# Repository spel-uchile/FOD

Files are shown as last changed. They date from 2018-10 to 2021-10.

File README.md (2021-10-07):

# Femto-satellite Orbital Deployer (FOD)

This repository contains the PCB design and the source code of a femto-satellite orbital deployer or FOD. This device works by cutting a fishing line with Nichrome wire. The fishing line is normally pressing a hinge lever. When the line is cut, the hinge lever is released end the microcontroller can detect the release status.

The PCB has a transceiver (NRF24L01) to communicate with the femto-satellite once it is released. There is also a LED showing the release status, and a reset button. The energy and the comunication with the OBC is done through a molex cable with a picoblade connector.

This new version is designed for CubeSats of 2U or more. It is intended to be used as a type A interstage panel, so that it leaves more space inside the CubeSat for other payloads.

Current version: 4.0.0

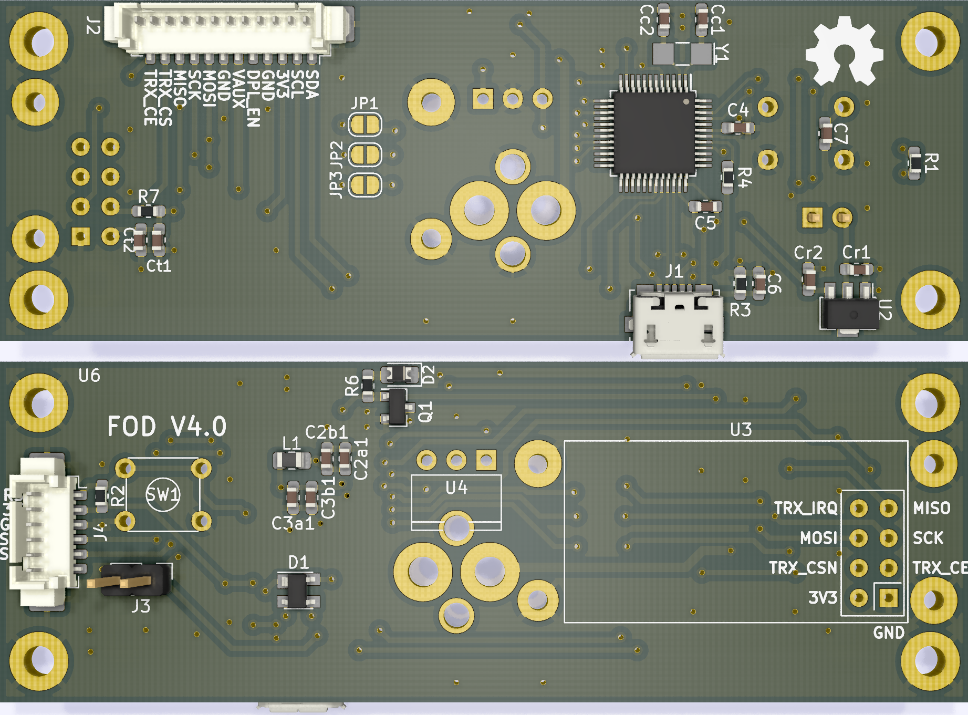
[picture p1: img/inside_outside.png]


### Supported software:

* KiCAD 5.99.0

### Supported hardware:

* Microcontroller: ATSAMD21G18
* Transceiver: NRF24L01
* Hinge lever: AV4524
* Mosfet: PMV16XNR

### Contact:

* Name: Matías Vidal Valladares
* e-mail: matias.vidal.v@gmail.com

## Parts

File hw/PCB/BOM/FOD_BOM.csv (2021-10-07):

Comment | Designator | Footprint | JLCPCB Part #
10uF 0603, C1608X5R0J106K080AE | C2a1, C3a1, Ct2 | Capacitor_SMD:C_0603_1608Metric_Pad1.05x0.95mm_HandSolder | C267437
100nF 0603, 06036C104JAT2A | C2b1, C3b1, C5, C7, Ct1 | Capacitor_SMD:C_0603_1608Metric_Pad1.05x0.95mm_HandSolder
1uF 0603, C0603X105J9RACAUTO | C4, Cr1, Cr2 | Capacitor_SMD:C_0603_1608Metric_Pad1.05x0.95mm_HandSolder
4.7nF 0603, C0603C472K9RACTU | C6 | Capacitor_SMD:C_0603_1608Metric_Pad1.05x0.95mm_HandSolder
9pF 0603, 06033A9R0CAT2A | Cc1, Cc2 | Capacitor_SMD:C_0603_1608Metric_Pad1.05x0.95mm_HandSolder
PRTR5V0U2X,215 | D1 | Package_TO_SOT_SMD:SOT-143 | C12333
Green LED 0805 | D2 | Diode_SMD:D_0805_2012Metric_Pad1.15x1.40mm_HandSolder | C397047
USB_B_Micro, ZX62-AB-5PA(31) | J1 | Connector_USB:USB_Micro-B_Molex_47346-0001 | C2692071
Molex PicoBlade SMD 1x12, 53398-1271 | J2 | Connector_Molex:Molex_PicoBlade_53398-1271_1x12-1MP_P1.25mm_Vertical
Pin header 1x2 | J3 | Connector_PinHeader_2.54mm:PinHeader_1x02_P2.54mm_Vertical
Molex PicoBlade SMD 1x6, 53398-0671 | J4 | Connector_Molex:Molex_PicoBlade_53398-0671_1x06-1MP_P1.25mm_Vertical
Jumper | JP1, JP2, JP3 | Jumper:SolderJumper-2_P1.3mm_Open_RoundedPad1.0x1.5mm
Ferrite_Bead, MPZ2012S221AT000 | L1 | Inductor_SMD:L_0805_2012Metric_Pad1.15x1.40mm_HandSolder | C76818
PMV16XNR | Q1 | Package_TO_SOT_SMD:SOT-23 | C110920
1k 0603, RC0603FR-071KL | R1, R7 | Resistor_SMD:R_0603_1608Metric_Pad1.05x0.95mm_HandSolder
10k 0603, ESR03EZPF1002 | R2 | Resistor_SMD:R_0603_1608Metric_Pad1.05x0.95mm_HandSolder | C253330
1M 0603, ESR03EZPF1004 | R3 | Resistor_SMD:R_0603_1608Metric_Pad1.05x0.95mm_HandSolder | C253332
330, CRGH0603F330R | R4, R6 | Resistor_SMD:R_0603_1608Metric_Pad1.05x0.95mm_HandSolder
Reset_push | SW1 | Button_Switch_THT:SW_TH_Tactile_Omron_B3F-10xx | C231317
ATSAMD21G18A-AFT | U1 | Package_QFP:TQFP-48_7x7mm_P0.5mm | C78624
AP7215-33YG-13 | U2 | Package_TO_SOT_SMD:SOT-89-3 | C460367
AV4524 | U4 | Interrupt:AV4524
32.768kHz, ECS-.327-9-34QCS-TR | Y1 | Crystal:Crystal_SMD_EuroQuartz_EQ161-2Pin_3.2x1.5mm_HandSoldering

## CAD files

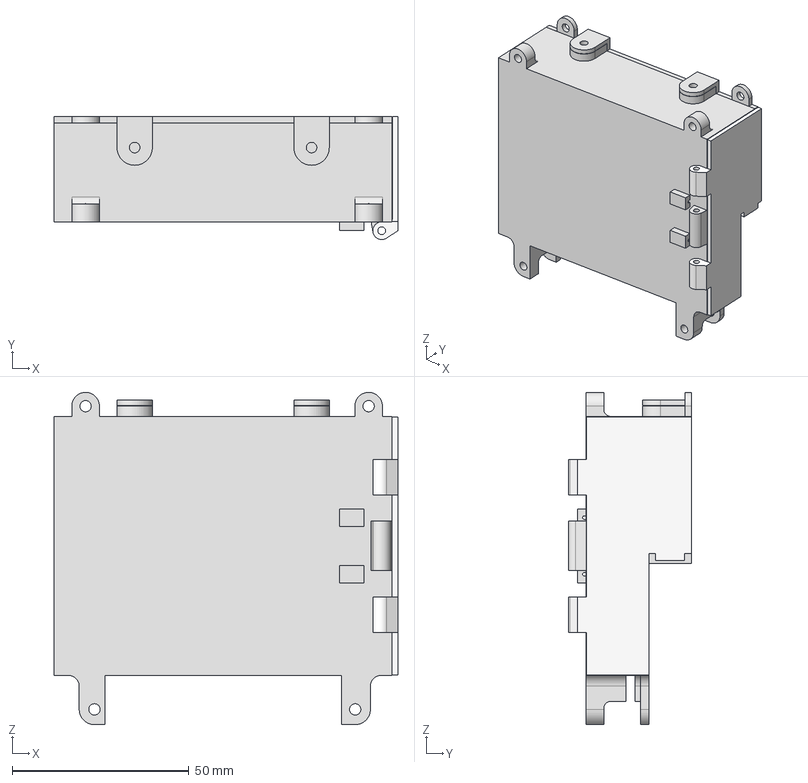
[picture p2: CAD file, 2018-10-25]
hw/CAD/Ensamble_rev1.stp
97.2 x 34.8 x 93.9 mm
Base_FOD
Tapa_FOD
Tapa_frental_FOD

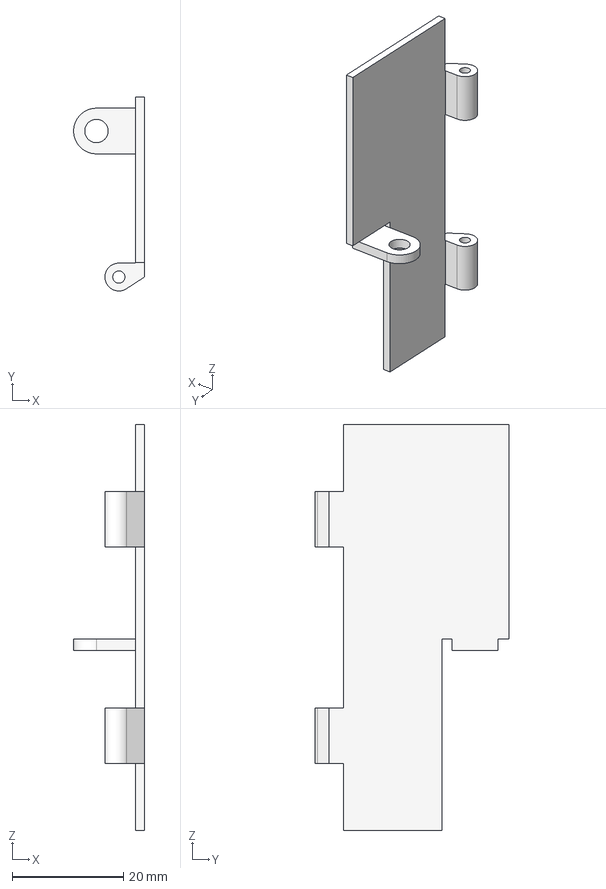
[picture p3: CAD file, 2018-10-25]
hw/CAD/Tapa_FOD.stp
12.7 x 34.8 x 72.8 mm

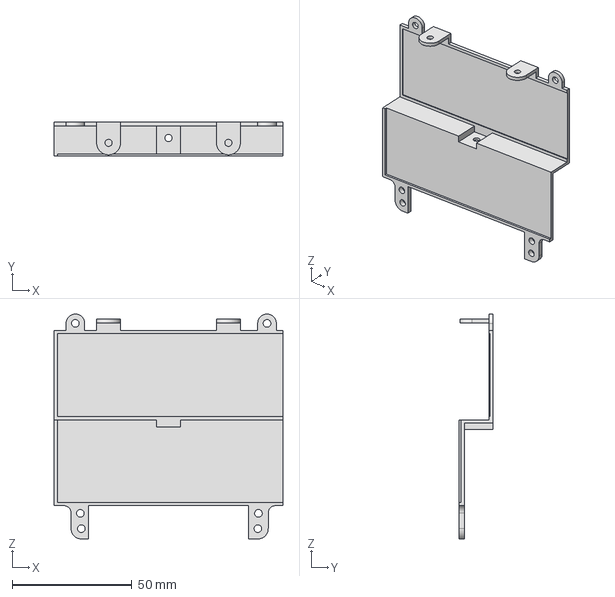
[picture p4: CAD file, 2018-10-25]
hw/CAD/Techo_FOD.stp
95.6 x 14.4 x 93.9 mm

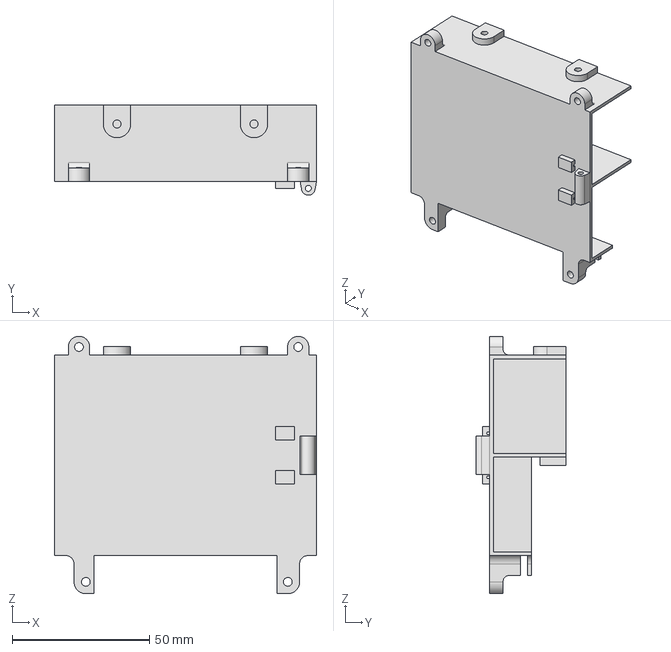
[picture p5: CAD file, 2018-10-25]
hw/CAD/Base_FOD.stp
95.6 x 33.0 x 93.9 mm

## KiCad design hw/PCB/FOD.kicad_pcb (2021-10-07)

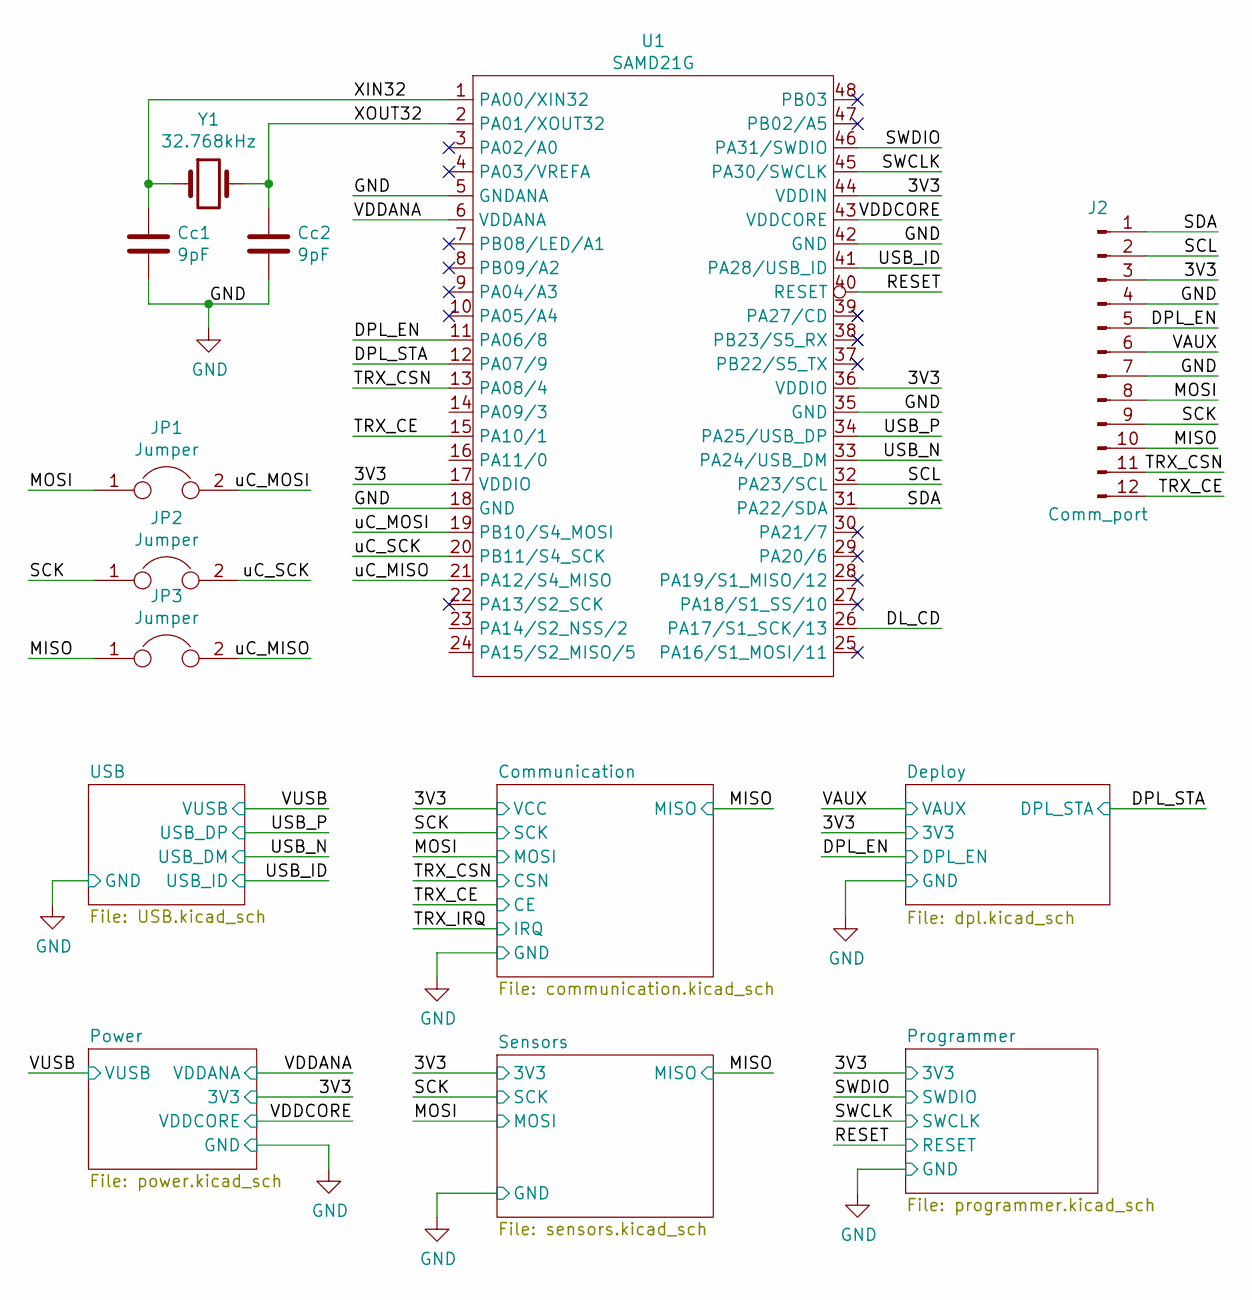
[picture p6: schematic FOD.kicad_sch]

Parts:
Cc1, Cc2: 9pF; C_0603_1608Metric_Pad1.05x0.95mm_HandSolder
J2: Comm_port; Molex_PicoBlade_53398-1271_1x12-1MP_P1.25mm_Vertical
JP1, JP2, JP3: Jumper; SolderJumper-2_P1.3mm_Open_RoundedPad1.0x1.5mm
U1: SAMD21G; TQFP-48_7x7mm_P0.5mm
Y1: 32.768kHz; Crystal_SMD_EuroQuartz_EQ161-2Pin_3.2x1.5mm_HandSoldering

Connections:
/3V3: J2.3, U1.17 (VDDIO), U1.36 (VDDIO), U1.44 (VDDIN); also elsewhere on the board
/DL_CD: U1.26 (PA17/S1_SCK/13)
/DPL_EN: J2.5, U1.11 (PA06/8); also elsewhere on the board
/DPL_STA: U1.12 (PA07/9); also elsewhere on the board
/MISO: J2.10, JP3.1; also elsewhere on the board
/MOSI: J2.8, JP1.1; also elsewhere on the board
/RESET: U1.40 (RESET); also elsewhere on the board
/SCK: J2.9, JP2.1; also elsewhere on the board
/SCL: J2.2, U1.32 (PA23/SCL)
/SDA: J2.1, U1.31 (PA22/SDA)
/SWCLK: U1.45 (PA30/SWCLK); also elsewhere on the board
/SWDIO: U1.46 (PA31/SWDIO); also elsewhere on the board
/TRX_CE: J2.12, U1.15 (PA10/1); also elsewhere on the board
/TRX_CSN: J2.11, U1.13 (PA08/4); also elsewhere on the board
/USB_ID: U1.41 (PA28/USB_ID); also elsewhere on the board
/USB_N: U1.33 (PA24/USB_DM); also elsewhere on the board
/USB_P: U1.34 (PA25/USB_DP); also elsewhere on the board
/VAUX: J2.6; also elsewhere on the board
/VDDANA: U1.6 (VDDANA); also elsewhere on the board
/VDDCORE: U1.43 (VDDCORE); also elsewhere on the board
/XIN32: Cc1.1, U1.1 (PA00/XIN32), Y1.1
/XOUT32: Cc2.1, U1.2 (PA01/XOUT32), Y1.2
/uC_MISO: JP3.2, U1.21 (PA12/S4_MISO)
/uC_MOSI: JP1.2, U1.19 (PB10/S4_MOSI)
/uC_SCK: JP2.2, U1.20 (PB11/S4_SCK)
GND: Cc1.2, Cc2.2, J2.4, J2.7, J2.MP, U1.5 (GNDANA), U1.18 (GND), U1.35 (GND), U1.42 (GND); also elsewhere on the board

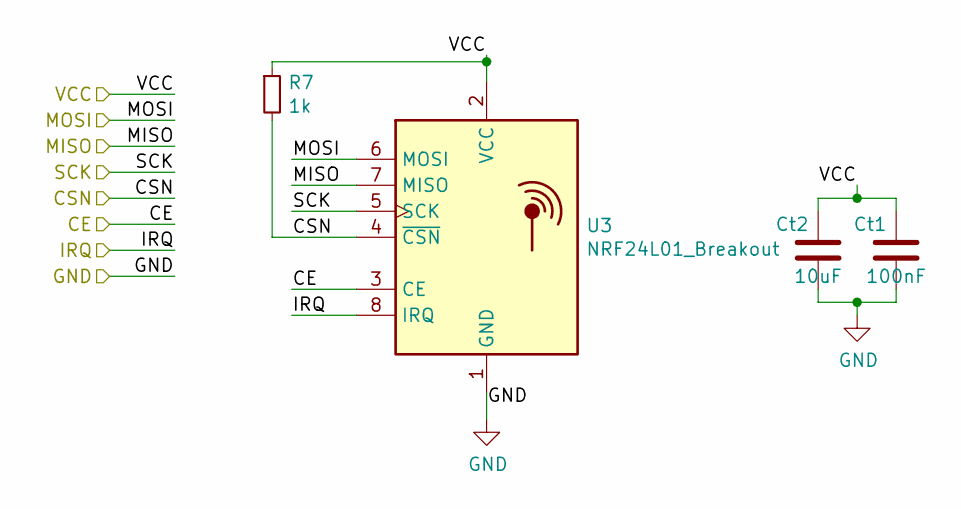
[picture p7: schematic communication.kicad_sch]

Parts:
Ct1: 100nF; C_0603_1608Metric_Pad1.05x0.95mm_HandSolder
Ct2: 10uF; C_0603_1608Metric_Pad1.05x0.95mm_HandSolder
R7: 1k; R_0603_1608Metric_Pad1.05x0.95mm_HandSolder
U3: NRF24L01_Breakout; nRF24L01_Breakout

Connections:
/3V3: Ct1.2, Ct2.2, R7.1, U3.2 (VCC); also elsewhere on the board
/MISO: U3.7 (MISO); also elsewhere on the board
/MOSI: U3.6 (MOSI); also elsewhere on the board
/SCK: U3.5 (SCK); also elsewhere on the board
/TRX_CE: U3.3 (CE); also elsewhere on the board
/TRX_CSN: R7.2, U3.4 (~CSN); also elsewhere on the board
/TRX_IRQ: U3.8 (IRQ)
GND: Ct1.1, Ct2.1, U3.1 (GND); also elsewhere on the board

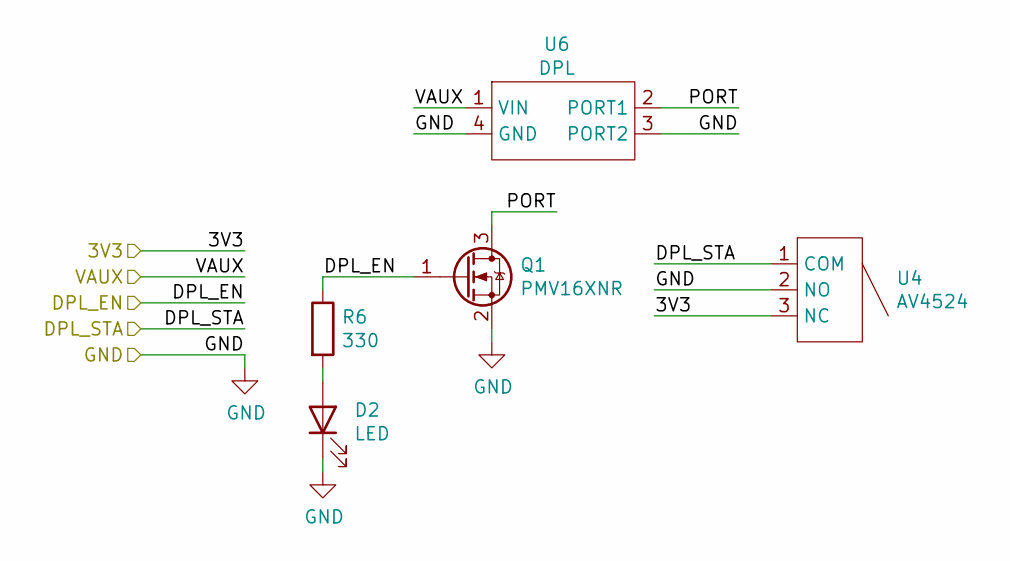
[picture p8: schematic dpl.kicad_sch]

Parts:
D2: LED; D_0805_2012Metric_Pad1.15x1.40mm_HandSolder
Q1: PMV16XNR; SOT-23
R6: 330; R_0603_1608Metric_Pad1.05x0.95mm_HandSolder
U4: AV4524
U6: DPL; Type-A_middle_port

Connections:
/3V3: U4.3 (NC); also elsewhere on the board
/DPL_EN: Q1.1 (G), R6.1; also elsewhere on the board
/DPL_STA: U4.1 (COM); also elsewhere on the board
/Deploy/PORT: Q1.3 (D), U6.2 (PORT1)
/VAUX: U6.1 (VIN); also elsewhere on the board
GND: D2.1 (K), Q1.2 (S), U4.2 (NO), U6.3 (PORT2), U6.4 (GND); also elsewhere on the board
unnamed: D2.2 (A), R6.2

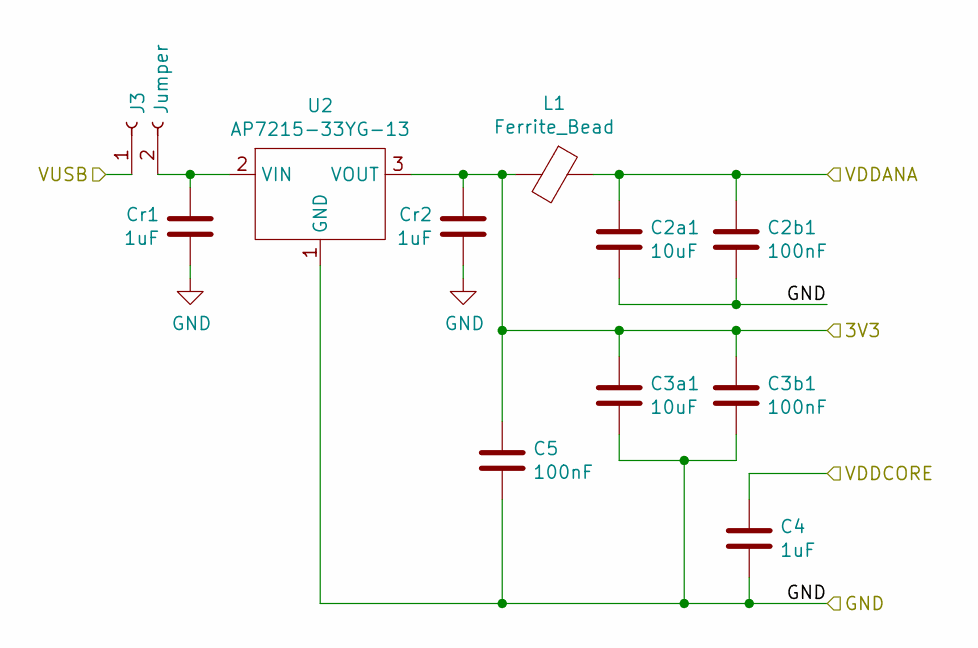
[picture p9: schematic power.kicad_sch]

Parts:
C2a1, C3a1: 10uF; C_0603_1608Metric_Pad1.05x0.95mm_HandSolder
C2b1, C3b1, C5: 100nF; C_0603_1608Metric_Pad1.05x0.95mm_HandSolder
C4: 1uF; C_0603_1608Metric_Pad1.05x0.95mm_HandSolder
Cr1, Cr2: 1uF; C_0603_1608Metric_Pad1.05x0.95mm_HandSolder
J3: Jumper; PinHeader_1x02_P2.54mm_Vertical
L1: Ferrite_Bead; L_0805_2012Metric_Pad1.15x1.40mm_HandSolder
U2: AP7215-33YG-13; SOT-89-3

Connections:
/3V3: C3a1.1, C3b1.1, C5.1, Cr2.1, L1.2, U2.3 (VOUT); also elsewhere on the board
/VDDANA: C2a1.1, C2b1.1, L1.1; also elsewhere on the board
/VDDCORE: C4.1; also elsewhere on the board
/VUSB: J3.1; also elsewhere on the board
GND: C2a1.2, C2b1.2, C3a1.2, C3b1.2, C4.2, C5.2, Cr1.2, Cr2.2, U2.1 (GND); also elsewhere on the board
unnamed: Cr1.1, J3.2, U2.2 (VIN)

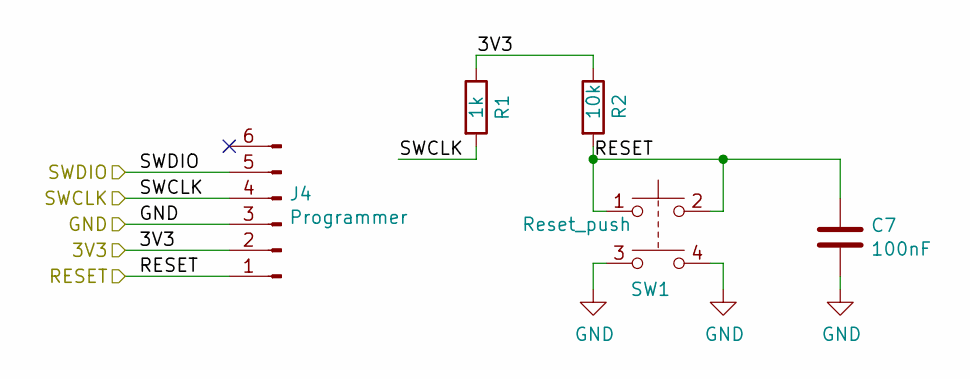
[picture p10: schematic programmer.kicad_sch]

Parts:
C7: 100nF; C_0603_1608Metric_Pad1.05x0.95mm_HandSolder
J4: Programmer; Molex_PicoBlade_53398-0671_1x06-1MP_P1.25mm_Vertical
R1: 1k; R_0603_1608Metric_Pad1.05x0.95mm_HandSolder
R2: 10k; R_0603_1608Metric_Pad1.05x0.95mm_HandSolder
SW1: Reset_push; SW_TH_Tactile_Omron_B3F-10xx

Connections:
/3V3: J4.2, R1.1, R2.1; also elsewhere on the board
/RESET: C7.1, J4.1, R2.2, SW1.1, SW1.2; also elsewhere on the board
/SWCLK: J4.4, R1.2; also elsewhere on the board
/SWDIO: J4.5; also elsewhere on the board
GND: C7.2, J4.3, J4.MP, SW1.3, SW1.4; also elsewhere on the board

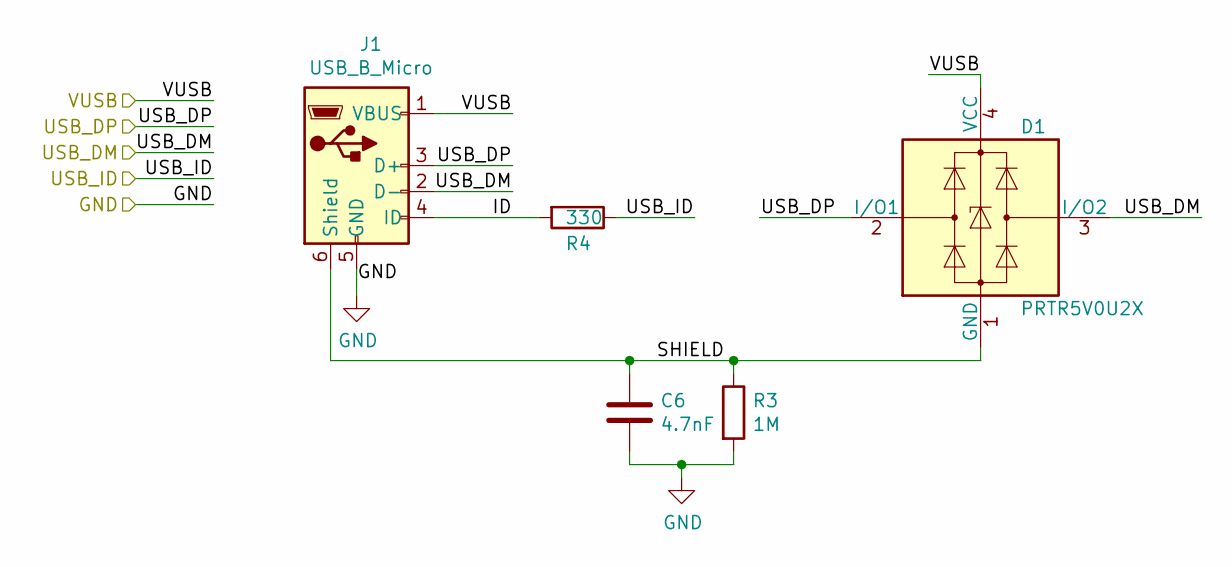
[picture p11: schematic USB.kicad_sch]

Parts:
C6: 4.7nF; C_0603_1608Metric_Pad1.05x0.95mm_HandSolder
D1: PRTR5V0U2X; SOT-143
J1: USB_B_Micro; USB_Micro-B_Molex_47346-0001
R3: 1M; R_0603_1608Metric_Pad1.05x0.95mm_HandSolder
R4: 330; R_0603_1608Metric_Pad1.05x0.95mm_HandSolder

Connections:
/USB/ID: J1.4 (ID), R4.2
/USB/SHIELD: C6.1, D1.1 (GND), J1.6 (Shield), R3.1
/USB_ID: R4.1; also elsewhere on the board
/USB_N: D1.3 (I/O2), J1.2 (D-); also elsewhere on the board
/USB_P: D1.2 (I/O1), J1.3 (D+); also elsewhere on the board
/VUSB: D1.4 (VCC), J1.1 (VBUS); also elsewhere on the board
GND: C6.2, J1.5 (GND), R3.2; also elsewhere on the board

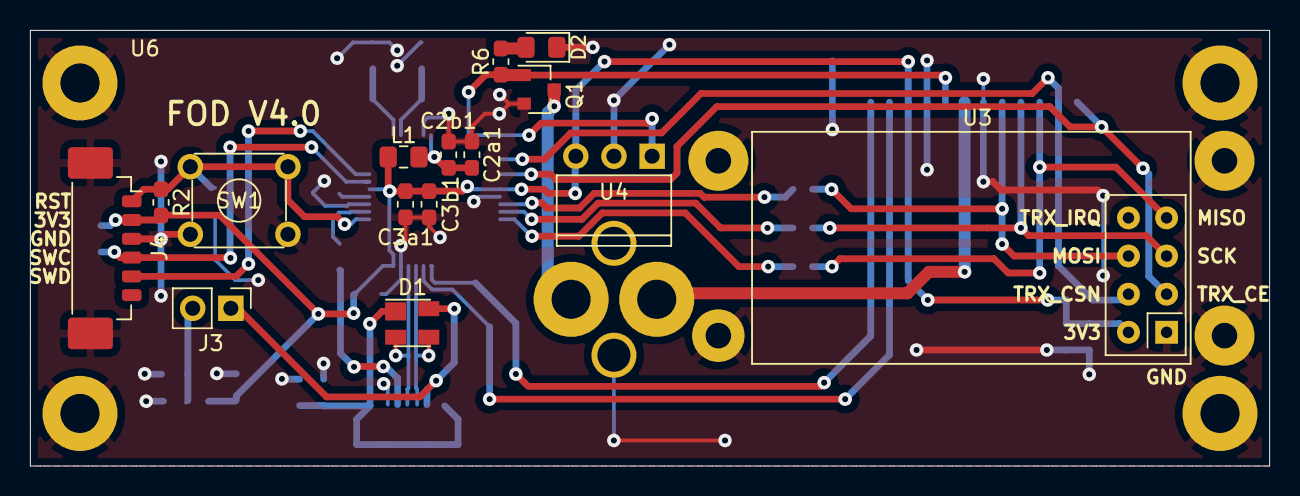
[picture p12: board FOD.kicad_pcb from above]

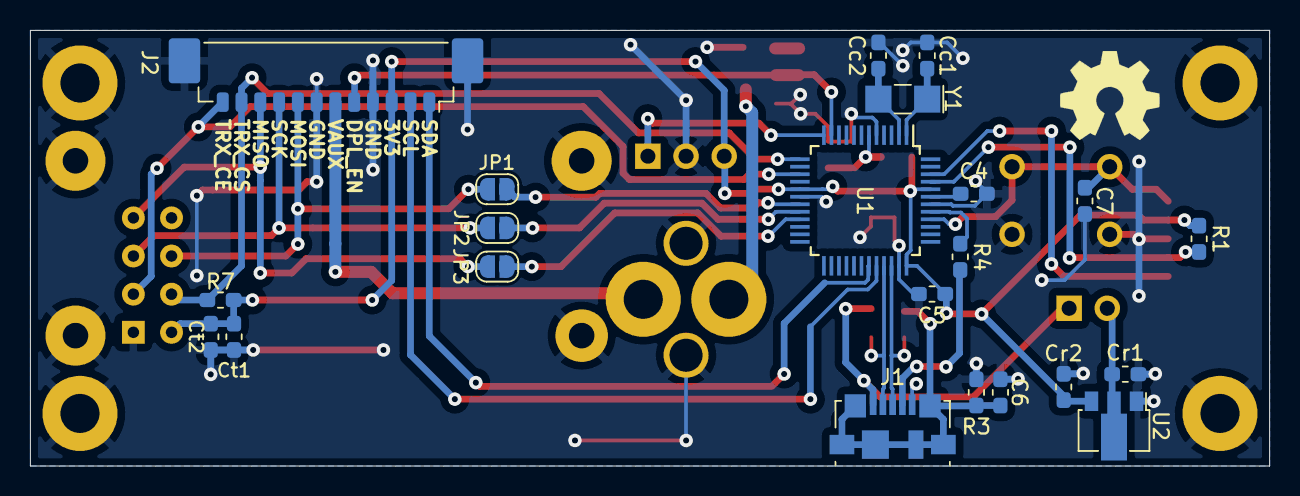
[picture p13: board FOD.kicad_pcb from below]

Board: 2 copper layers, 82.5 x 29.0 mm, 38 parts (22 on the bottom side), 31 nets.

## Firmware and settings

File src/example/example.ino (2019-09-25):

/**
 * @brief Femto-satellite v2.0
 */
 
/*Author: Matias Vidal*/

#include "FOD.h"
#include "radio.h"
#include "cmds.h"
#include <Wire.h>

#define CLIENT_ADDRESS 1
#define SERVER_ADDRESS 2
#define I2C_ADDRESS 7

/*Object Definitions*/
FOD fod;
Radio radio(RADIO_SLAVESELECTPIN, RADIO_INTERRUPT, RADIO_RST, CLIENT_ADDRESS, SERVER_ADDRESS);

// ================================================================
// ===                      INITIAL SETUP                       ===
// ================================================================

char buf[100];
char params[100];
int cmd = 0;

void setup() {
    // Initialize serial communication
    delay(1000);
    SerialUSB.begin(115200);
    SerialUSB.setTimeout(200);
    while (!SerialUSB) {
        ; // wait for serial port to connect.
    }
    // Initialize FOD's systems
    SerialUSB.println("Initializing FOD");
    fod.init();
    radio.init();
    Wire.begin(I2C_ADDRESS);
    Wire.onReceive(receiveHandler);
    Wire.onRequest(requestHandler);
    SerialUSB.println("Done.");
}

// ================================================================
// ===                    MAIN PROGRAM LOOP                     ===
// ================================================================

void loop() {
    if (SerialUSB.available()) {
	int i = 0;
    	while (SerialUSB.available()) {
    	    buf[i] = SerialUSB.read();
	    i++;
	}
	buf[i] = 0;
	sscanf(buf, "%d %[^\n]s", &cmd, &params);
    	executeCommand(cmd, params);
    }
    delay(10);
}

/**
 * I2C comunication handler between the FOD
 * and the OBC. This is used when the master
 * sends a command or instruction to the FOD.
 * @param Number of bytes read from the OBC.
 */
void receiveHandler(int numBytes) {
    int i = 0;
    while (Wire.available()) {
	buf[i] = Wire.read();
	i++;
    }
    buf[i] = 0;
    sscanf(buf, "%d %[^\n]s", &cmd, &params);
    executeCommand(cmd, params); 
}

/**
 * I2C request handler. This function is used
 * when the master asks the FOD to send data
 * back to him.
 */
void requestHandler() {
    SerialUSB.print("Received request: ");
    SerialUSB.print(cmd);
    SerialUSB.print("   Command: ");
    if (cmd == GET_CONFIG) {
	SerialUSB.println("GET_CONFIG");
	int ver_int = int(fod.version);
	int ver_dec = (fod.version - ver_int)*10;
	sprintf(buf, "%d.%d %d %d %d",
		ver_int, ver_dec, (int)fod.status(),
		fod.on_time, fod.attempts);
	Wire.write(buf);
	SerialUSB.print("Sent: ");
	SerialUSB.println(buf);
    }
    else if (cmd == FOD_GET_STATUS) {
	SerialUSB.println("FOD_GET_STATUS");
	if (fod.status()) {
	    Wire.write('1');
	    SerialUSB.print("Sent: ");
	    SerialUSB.println(1);
	}
	else {
	    Wire.write('0');
	    SerialUSB.print("Sent: ");
	    SerialUSB.println(0);
	}
    else if (cmd == GET_VERSION) {
	SerialUSB.println("GET_VERSION");
	int ver_int = int(fod.version);
	int ver_dec = (fod.version - ver_int)*10;
	sprintf(buf, "%d.%d", ver_int, ver_dec);
	Wire.write(buf);
	SerialUSB.print("Sent: ");
	SerialUSB.println(buf);
    }
    else {
	SerialUSB.print(cmd);
	SerialUSB.println(" is not available yet");
	Wire.write(cmd);
    }
    cmd = 12;
}

/**
 * Enables the low power mode of operation
 * of the FOD.
 * Currently it only puts the radio to sleep,
 * but it is expected to also put the
 * microcontroller into this state.
 * @return True if succesfull.
 */
bool lowPowerMode() {
    SerialUSB.println("Low power mode selected");
    return radio.lowPowerMode();
}

/**
 * Enables the normal mode of operation.
 */
void normalMode() {
    SerialUSB.println("Normal mode selected");
    radio.normalMode();
}

/**
 * This function displays all the FOD's commands.
 * These commands are the same for both the user
 * (via serial) and the OBC (via I2C).
 */
void help() {
    SerialUSB.println(F("Available commands:"));
    SerialUSB.print(UPDATE_DATA);
    SerialUSB.println(F(": UPDATE_DATA"));
    SerialUSB.print(SEND_BEACON);
    SerialUSB.println(F(": SEND_BEACON"));
    SerialUSB.print(DEPLOY_FEMTOSATS);
    SerialUSB.println(F(": DEPLOY_FEMTOSATS"));
    SerialUSB.print(FOD_GET_STATUS);
    SerialUSB.println(F(": FOD_GET_STATUS"));
    SerialUSB.print(SEND_FEMTOSAT_DATA);
    SerialUSB.println(F(": SEND_FEMTOSAT_DATA"));
    SerialUSB.print(SET_ON_TIME);
    SerialUSB.println(F(": SET_ON_TIME"));
    SerialUSB.print(GET_CONFIG);
    SerialUSB.println(F(": GET_CONFIG"));
    SerialUSB.print(GET_VERSION);
    SerialUSB.println(F(": GET_VERSION"));
    SerialUSB.print(ENABLE_LOW_POWER_MODE);
    SerialUSB.println(F(": ENABLE_LOW_POWER_MODE"));
    SerialUSB.print(DISABLE_LOW_POWER_MODE);
    SerialUSB.println(F(": DISABLE_LOW_POWER_MODE"));
    SerialUSB.print(HELP);
    SerialUSB.println(F(": HELP"));
}

/**
 * Executes a command received with its corresponding parameters.
 * @param cmd: Int with the command number.
 * @param params: A char array containing all the parameters.
 */
void executeCommand(int cmd, char params[]) {
    SerialUSB.print("Received: ");
    SerialUSB.print(cmd);
    SerialUSB.print("   Command: ");
    if (cmd == UPDATE_DATA) {
        SerialUSB.print("UPDATE_DATA");
	SerialUSB.print("   Parameters: ");
	SerialUSB.println(params);
        fod.updateData(params);
        SerialUSB.print("Data: ");
        SerialUSB.print("HH:MM:SS: ");
        SerialUSB.print(fod.gpsData.hour);
        SerialUSB.print(":");
        SerialUSB.print(fod.gpsData.minute);
        SerialUSB.print(":");
        SerialUSB.print(fod.gpsData.second);
        SerialUSB.print("    Sat: ");
        SerialUSB.print(fod.gpsData.satellites);
        SerialUSB.print("    Location: ");
        SerialUSB.print(fod.gpsData.latitude, 6);
        SerialUSB.print(",");
        SerialUSB.print(fod.gpsData.longitude, 6);
        SerialUSB.print("    Altitude (GPS): ");
        SerialUSB.println(fod.gpsData.altitude, 6);
    }
    else if (cmd == SEND_BEACON) {
	SerialUSB.println("SEND_BEACON");
    	radio.updateBeacon(&fod.gpsData);
    	radio.send_data();
    }
    else if (cmd == DEPLOY_FEMTOSATS) {
    	SerialUSB.println("DEPLOY_FEMTOSATS");
    	fod.deploy();
	SerialUSB.print("Deployment complete at ");
    	SerialUSB.print(fod.dt);
    	SerialUSB.println(" ms");
    }
    else if (cmd == FOD_GET_STATUS) {
	SerialUSB.println("FOD_GET_STATUS");
        SerialUSB.print("Released: ");
        SerialUSB.println(fod.status());    
    }
    else if (cmd == SEND_FEMTOSAT_DATA) {
    	SerialUSB.println("SEND_FEMTOSAT_DATA");
    	radio.updateBeacon(&fod.gpsData);
    	radio.send_data();
    }
    else if (cmd == SET_ON_TIME) {
        SerialUSB.print("SET_ON_TIME");
	SerialUSB.print("   Parameters: ");
	SerialUSB.println(params);
        fod.setOnTime(params);
        SerialUSB.print("New on time: ");
        SerialUSB.print(fod.on_time);
        SerialUSB.println(" ms");
    }
    else if (cmd == GET_CONFIG) {
        SerialUSB.println("GET_CONFIG");
        SerialUSB.print("Version: ");
        SerialUSB.print(fod.version, 1);
        SerialUSB.print("   Released: ");
        SerialUSB.print(fod.status());
        SerialUSB.print("   On time: ");
        SerialUSB.print(fod.on_time);
        SerialUSB.print(" ms   Attempts: ");
        SerialUSB.println(fod.attempts);
    }
    else if (cmd == GET_VERSION) {
        SerialUSB.println("GET_VERSION");
        SerialUSB.print("Current version is: ");
        SerialUSB.println(fod.version);
    }
    else if (cmd == ENABLE_LOW_POWER_MODE) {
    	SerialUSB.println("ENABLE_LOW_POWER_MODE");
    	lowPowerMode();
    }
    else if (cmd == DISABLE_LOW_POWER_MODE) {
	SerialUSB.println("DISABLE_LOW_POWER_MODE");
    	normalMode();
    }
    else if (cmd == HELP) {
	SerialUSB.println("HELP");
    	help();
    }
    else if (cmd == 12) {
        SerialUSB.println("DONE");
    }
    else {
        SerialUSB.print(cmd);
        SerialUSB.println(" is not available yet");
    }
}

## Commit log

2018-10-25 Added a basic PCB schematic.
    [Femtosat.sch, USB.sch, communication.sch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]
2018-10-25 CAD files
    CAD files
    [Base_FOD.stp, Ensamble_rev1.stp, Tapa_FOD.stp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]
2018-10-26 Added preliminary design of the PC104 board connections.
    [FOD.kicad_pcb, FOD.sch, USB.sch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]
2018-11-09 Updated the FOD's PCB.
2018-11-12 Added deploy system to schematic.
    [dpl.sch]
2018-11-12 Updated PCB's schematic.
    [FOD.kicad_pcb, FOD.sch, USB.sch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]
2018-11-12 Added pin labels for the femto-satellite deploy system.
    [FOD.sch, dpl.sch]
2018-11-14 Improved the FOD's PCB boundaries based on the new payload standard for the SUCHAI 2 and 3. Added silk mask for the stack and the holes. Added space for better cable management.
2018-11-14 Updated the connections and the footprints asignation.
    [FOD.kicad_pcb, FOD.sch, dpl.sch]
2018-11-15 Created library for the high power resistor used in the deploy system.
2018-11-15 Added the deployment system to the board's footprint.
    [FOD.kicad_pcb, FOD.sch, USB.sch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]
2018-11-15 Added a library for the SAMD21 microcontroller and for a power regulator.
2018-11-16 Changed outer line from the libraries to Edge.Cuts. Increased the drill size of the mechanical holes.
    [FOD.kicad_pcb]
2018-11-19 Added new connections and 3D models. Most components are now placed in the PCB.
    [FOD.kicad_pcb, FOD.sch, communication.sch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]
2018-11-20 Fixed error in edge cuts, and updated the pads' size of the mechanical holes.
2018-11-20 Added preliminary CAD design of the FOD's PCB.
2018-11-20 Fixed error in pin spacing (changed from 2.56 mm to 2.54 mm).
    [FOD.kicad_pcb]
2018-11-20 Fixed some dimensions of the FOD's PCB.
    [FOD.kicad_pcb]
2018-11-20 Updated the preliminary FOD's PCB CAD.
2018-11-21 Added switch to detect the deplyment status. Routed all connections.
    [FOD.kicad_pcb, FOD.sch, dpl.sch]
2018-11-22 Made space for the interrupter.
    [FOD.kicad_pcb]
2018-11-22 Fixed space conflict between the interrupter and the voltage regulator.
    [FOD.kicad_pcb]
2018-11-28 Changed the NPTH holes to Through-holes to connect them to ground.
2018-11-28 Updated the PCB with the thorugh-holes connected to ground.
    [FOD.drl, FOD.gbl, FOD.gbo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]
2018-11-28 Exported PCB's CAD model.
2018-11-28 Added silk layer with pin labels.
    [FOD.kicad_pcb]
2018-11-28 Ploted new gerber files.
    [FOD.drl, FOD.gbl, FOD.gbo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]
2018-11-28 Reduced the size of some drill holes.
2018-11-28 Exported the corrected version of the PCB in Step file format.
2019-06-05 Updated the RFM69HCW symbol and created a new SAMD21E symbol.
    [FOD.sch, USB.sch, communication.sch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]
2019-06-14 Increased drill and pad size for the PC104 stack.
2019-06-14 Increased PC104 pad's and drill's size.
2019-07-05 Updated the symbol and footprint of the PC104 standard.
2019-07-08 Finished preliminary design phase for the version 2.0.
    [FOD.kicad_pcb, FOD.sch, USB.sch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]
2019-07-09 Replaced the SMA connector with an U.FL connector. Added some layout improvements.
    [FOD.kicad_pcb, FOD.sch, USB.sch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]
2019-07-09 Moved the drill holes for the nylon wire. Generated the Gerber files.
    [FOD.drl, FOD.gbl, FOD.gbo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]
2019-07-09 Generated a new CAD file for the 2.0 version of the PCB.
2019-07-11 Added a label for the deployment status LED.
    [FOD.kicad_pcb]
2019-07-12 Reploted the gerber files to add a silk label.
    [FOD.drl, FOD.gbl, FOD.gbo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]
2019-07-12 Added a new CAD file for the femto-satellite orbital deployer v2.0.
2019-07-18 Moved some missplaced silk labels.
    [FOD.kicad_pcb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]
2019-07-18 New CAD for the FOD.
2019-07-18 Fixed a small issue about the pin assignation of the deployment sensor. Change the position of some vias so that they are not too close to some tracks.
    [FOD.kicad_pcb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]
2019-07-19 Fixed multiple errors in the FOD class and in the arduino file.
    [example.ino]
2019-07-19 Enlarged the drill hole and the pad's size of the interrupter.
    [FOD.kicad_pcb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]
2019-07-19 Exported new CAD file.
2019-08-02 Fixed and added functions to change the mode of operation of the FOD. For now it only affects the transceiver.
    [example.ino]
2019-08-05 Added more modes of operation. Fixed some minor errors.
    [example.ino]
2019-08-28 Fixed some errors and added serial commands.
    [example.ino]
2019-09-03 Added more commands to adjust the on time and to receive gps data from I2C or Serial communication.
2019-09-18 Implemented a function that handles the received commands, Serial and I2C. Changed the way the method setOnTime works.
2019-09-23 Solved some compilation errors due to old struct parameters that were deprecated.
    [example.ino]
2019-09-24 Fixed errors in the I2C communication. Added more parameters to send to the OBC such as the current on-time and the number of attempts
    [example.ino]
2019-09-25 Added a delay at the start of the program for stability.
    [example.ino]
2020-03-22 Created a new PCB for the Femto-satellite Orbital Deployer (FOD). Instead of using the PC104 standard, it now has the shape of a type A interstage panel. Added a data logger. Deleted old files from t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
    [FOD.kicad_pcb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]
2020-03-22 Created a new CAD for the 3.0 version. Deleted old CAD.
2020-03-26 Improved the trace routing to increase the ground plane. Added text labels for some connectors.
    [FOD.kicad_pcb]
2020-03-26 Generated new gerber files. Updated the step file.
    [FOD_v3.drl, FOD_v3.gbl, FOD_v3.gbo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]
2020-03-27 Separated the VIN power line into two independent power lines (VAUX and VAUX2). This is done to add compatibility with other CubeSats standards. Added the option to bridge those lines with a zero Ohm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
    [FOD.kicad_pcb, FOD.sch, dpl.sch]
2020-03-27 Generated new gerber and CAD files.
    [FOD_v3.drl, FOD_v3.gbl, FOD_v3.gbo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]
2021-10-07 Added an image for the new PCB version and updated the README file.
2021-10-07 Updated the gerber files.
    [FOD_v3.drl, FOD_v3.gbl, FOD_v3.gbo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]
2021-10-07 FOD's new PCB version.
    [FOD.kicad_pcb, communication.sch]
2021-10-07 New files for the new FOD PCB.
    [FOD.kicad_sch, USB.kicad_sch, communication.kicad_sch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]
2021-10-07 Removed the data logger and updated the libraries.
    [data_logger.sch]
2021-10-07 Deleted old files and added a BOM.
    [FOD.kicad_sch, FOD.sch, FOD_BOM.csv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]
2021-10-07 Updated the CAD file.
